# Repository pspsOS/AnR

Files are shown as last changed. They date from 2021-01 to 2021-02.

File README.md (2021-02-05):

# AnR: PSPS Avionics and Recovery GitHub
This document was last edited by Jeffrey Kaji on *4 Feb 2021*. <br/>
View our license [here](LICENSE)

## MITCH_2021
**Multi-Instrument Telemetry Computer Hardware** for PSPS 2021 Rocket<br> 
Important Macros: <br>
``getBit(A, X)`` : gets the *"Xth"* bit of *"A"*. _(By VV)_<br>
``setBit(A, X, V)`` : sets the *"Xth"* bit of *"A"* to *"V"*. _(By VV)_ <br><br>
Debuging Macros: <br>
``print()`` : Prints to console. Is disabled by ``NDEBUG``. Does not accept string formatters. _(By JK)_ <br>
``prints()`` : Prints to console. Is disabled by ``NDEBUG``. Requires string formatters. _(By JK)_ <br>
``printe()`` : Prints to error stream. Is disabled by ``NDEBUG``. Requires string formatters. _(By JK)_ <br>

#### Quick Links
* [Documentation Folder **Docs/**](../Docs/README.md)
* [**Recovery-Avionics Jira**](https://psps-recovery-avionics.atlassian.net/jira/software/projects/AV/boards/2)
* [**SRAD Software Confluence Page**](https://psps-recovery-avionics.atlassian.net/wiki/spaces/PSPS/pages/31457281/SRAD+Software)
* [**Task Flowcharts Google Drive Folder**](https://drive.google.com/drive/u/0/folders/1KGmiUlNgTaysgdSle6QIzn_O4cT77nek)
* [**Hardware Datasheets Google Drive Folder**](https://drive.google.com/drive/u/0/folders/14jC0XhoOVIF4Ko5ylgHbCWUhaxgak8n0)

---
**Creating a *README.md*?** <br />
 Try using this free online editor that makes it super easy: 
<https://jbt.github.io/markdown-editor/>

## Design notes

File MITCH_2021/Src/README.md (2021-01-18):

# Src
### Generated Project Files:
* [__freertos.c__](freertos.c)
* [__main.c__](main.c)
* [__stm32f4xx_hal_msp.c__](stm32f4xx_hal_msp.c)
* [__stm32f4xx_hal_timebase_tim.c__](stm32f4xx_hal_timebase_tim.c)
* [__stm32f4xx_it.c__](stm32f4xx_it.c)
* [__sysmem.c__](sysmem.c)
* [__system_stm32f4xx.c__](system_stm32f4xx.c)

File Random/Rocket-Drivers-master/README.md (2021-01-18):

# Rocket Drivers

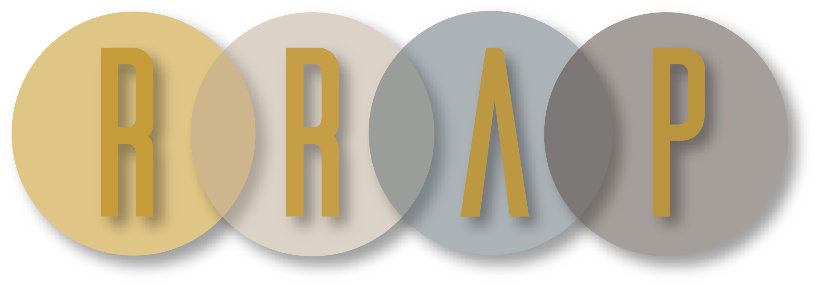
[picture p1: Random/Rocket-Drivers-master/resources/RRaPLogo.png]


This project contains files written to control the avionics platform for Reusable Rocketry at Purdue's gimbal based Atlas platform. The drivers are also intended for use in the Purdue Space Program's solid rocket program.

> ALL CODE IS PROVIDED AS IS. PLEASE READ THE LICENSE FOR MORE INFORMATION

## Timeline

- [x] Create generic SPI bus functions
- [X] Extract pressure, temperature, and altitude from onboard barometer
- [X] Extract (but not parse) NMEA strings from GPS
- [X] Extract linear accelerometer data
- [ ] Extract 9 axis IMU data

## Intended Hardware

These drivers are intended to be used in conjunction with 4 sensors. These sensors are:

- [MS5607-02BA03
Barometric Pressure Sensor](https://www.te.com/commerce/DocumentDelivery/DDEController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)
- [FGPMMOPA6H Standalone GPS Module](https://cdn-shop.adafruit.com/datasheets/GlobalTop-FGPMMOPA6H-Datasheet-V0A.pdf)
- [MMA655x Single Axis Inertial Sensor](https://www.nxp.com/docs/en/data-sheet/MMA655x.pdf)
- [ICM-20948 IMU](http://www.invensense.com/wp-content/uploads/2016/06/DS-000189-ICM-20948-v1.3.pdf)

## Notes

The struct `rocket_t` is my default data container. It should be changed to match whatever the intended plan for the rocket is. Doing this is simply easier from my end, so it isn't really a finalized solution. The calculations for the barometer are already included in the code. However, these would be worth going over again and starting to understand what they do and how they work. As for the GPS, the code will only return the NMEA strings GLL, GPRMC, and GPVTG (no sattelite count) unless something else is required. The command to change this frequency is 'PMTK_API_SET_NMEA_OUTPUT' and can be found [here](https://cdn-shop.adafruit.com/datasheets/PMTK_A11.pdf). The code will need to be changed to reflect the changes in output stings, but it shouldn't be too hard with the given code.

> `HandleHALError()` could be a very powerful tool for detecting issues. Since the target platform is unknown, it has been left blank. Please make sure to update this!

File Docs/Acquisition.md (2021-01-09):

# Acquisition
This document was last edited by Jeffrey Kaji on *5 Jan 2021*. <br/>

## Description
This is a documentation for the code supporting the task _Acquisition_. <br>
Created for use by Purdue Space Program Solids. <br><br>
[View][1] the _Task Flow Chart_. <br>

__Required Files:__
* [acquisition.h](../MITCH_2021/IncPSP/acquisition.h)
* [acquisition.c](../MITCH_2021/SrcPSP/acquisition.c)

[1]: https://drive.google.com/file/d/17b3zl4mSmjUOjUfPsQ9OTFR39xYNh1Iw/view?usp=sharing "Task Flow Chart (Read Only)"

## acquisition.h
_acquisition.h_ is a header file. A header file is a file with extension _.h_ which contains C function declarations and macro definitions to be shared between several source files. <br>
```c
// Parent Functions
void setup_A();
void loop_A();

// Setup
void gpsSetup_A();
void bmpSetup_A();
void imuSetup_A();
void alaSetup_A();

// Loop
void gpsRead_A();
void bmpRead_A();
void imuRead_A();
void checkStatus_A();
void sendUpdate_A();
``` 
The above is the main contents of _acquisition.h_. This declares all the functions created in _acquisition.c_.

## acquisition.c
_acquisition.c_ is a source file. A source file is a file with extension _.c_ that contains program instructions. <br> <br>
_acquisition.c_ acquires the raw data from the sensors and sends the data to processing via the global interface structs.

```c
/* Local variable declarations */
char gpsNmea[MAX_NMEA]; // Buffer that holds GPS String
bool daqScaling;        // Enables/Disables DAQ Scaling
ui8 daqScaler;          // DAQ Scaling number – Sets the ratio
bool gpsNominal;        // Indicates whether the GPS is nominal
bool bmpNominal;        // Indicates whether the BMP is nominal
bool imuNominal;        // Indicates whether the IMU is nominal
bool alaNominal;        // Indicates whether the ALA is nominal
bool sendDaqStatus;     // Indicates whether to update the daqStatusData struct
ui8 gpsCounter;         // Counter used in DAQ Scaling for Finite State Machine
ui8 bmpCounter;         // Counter used in DAQ Scaling for Finite State Machine
ui8 fsmState;           // Defines state of Finite State Machine

// Used for parsing NMEA data
ui8 _nmeaAddrStart;
ui8 _nmeaAddrEnd;

// File pointers for Debugging
#ifndef NDEBUG
	FILE *_gpsFile;
	FILE *_bmpFile;
	FILE *_imuFile;
	FILE *_alaFile;
#endif
```
The above declares the local variables. Listed below are the current variables:
* __gpsNmea[MAX_NMEA]__ is a character array (string) that holds the latest read from the GPS sensor. It is then parsed and passed to Processing by the function __gpsRead_A()__ via the struct __g_gpsData__. The constant __MAX_NMEA__ is defined in the header file [__common.h__](Common.md).
* __daqScaling__ is true when DAQ Scaling is enabled. DAQ Scaling makes _Acquisition_ act as a finite state machine, making measurments across the different sensors at different rates. 
* __daqScaler__ determines the ratios of data acquisition between each of the sensors. Let __daqScaler = n__ and assume DAQ Scaling is enabled. For each GPS measurment, _Acquisition_ will take __n__ BMP measurments and __n<sup>2</sup>__ IMU measurements.
* __gpsNominal__ is true if connection with the GPS has been established and if it is acting nominally.
* __bmpNominal__ is true if connection with the BMP has been established and if it is acting nominally.
* __imuNominal__ is true if connection with the IMU has been established and if it is acting nominally.
* __alaNominal__ is true if connection with the ALA has been established and if it is acting nominally.
* __sendDaqStatus__ is true if the DAQ Status struct should be updated.
* __gpsCounter__ is TBD
* __bmpCounter__ is TBD
* __fsmState__ is TBD
* **_nmeaAddrStart** is used when parsing NMEA strings. It stores the start index of a specific element within the string and is set by the the function [**_findNmeaAddr(int addr)**](###_findNmeaAddr(int-addr)).
*  **_nmeaAddrEnd** is used when parsing NMEA strings. It stores the end index of a specific element within the string and is set by the the function [**_findNmeaAddr(int addr)**](###_findNmeaAddr(int-addr)).
*  **_gpsFile** is a file pointer to the text file that has test data for the GPS. This is only declared if **NDEBUG** is not defined.
*  **_bmpFile** is a file pointer to the text file that has test data for the BMP. This is only declared if **NDEBUG** is not defined.
*  **_imuFile** is a file pointer to the text file that has test data for the IMU. This is only declared if **NDEBUG** is not defined.
*  **_alaFile** is a file pointer to the text file that has test data for the ALA. This is only declared if **NDEBUG** is not defined.
<br><br>

### setup_A()
```c
void setup_A() {

	// Initialize local variables
	daqScaling = false;
	daqScaler = DEFAULT_DAQ_SCALER;
	gpsNominal = false;
	bmpNominal = false;
	imuNominal = false;
	alaNominal = false;
	sendDaqStatus = false;
	gpsCounter = 0;
	bmpCounter = 0;
	fsmState = ACQUIRE_IMU_BMP_GPS;

	// Setup sensors
	gpsSetup_A();
	bmpSetup_A();
	imuSetup_A();
	alaSetup_A();

	// Unlock initialized interface structs
	g_daqStatusData.lock = false;
	g_daqScalingData.lock = false;
	
	// Send update
	sendUpdate_A();
}
```
The above function is the one-time setup function for _acquisition.c_. This function has different sections, each denoted by their own comment header. <br>
#### Intialize local variables
In this section, all local variables are initialized as needed.
```c
	daqScaling = false;
	daqScaler = DEFAULT_DAQ_SCALER;
```
> DAQ Scaling is disabled on startup. The DAQ Scaler is set to the default value constant which is defined in common.h.
<br><br>

```c
	gpsNominal = false;
	bmpNominal = false;
	imuNominal = false;
	alaNominal = false;
```
> All _"sensor nominal"_ variables are set to false. Each variable will be set to true once a connection to its sensor is established.
<br><br>

```c
	sendDaqStatus = false;
```
> Since __setup_A()__ already updates the DAQ Status interface struct, __sendDaqStatus__ is initially set to false.
<br><br>

```c
	gpsCounter = 0;
	bmpCounter = 0;
	fsmState = ACQUIRE_IMU_BMP_GPS;
```
> Finite state machine variables. TBD
<br><br>

#### Setup sensors
In this section, each sensor is setup by calling their setup functions.
```c
	gpsSetup_A();
	bmpSetup_A();
	imuSetup_A();
	alaSetup_A();
```

#### Unlock initialized interface structs
In this section, the initialized global interface structs used by _Acquisition_ are unlocked, insuring they can be accessed.
```c
	g_daqStatusData.lock = false;
	g_daqScalingData.lock = false;
```
#### Send update
The DAQ Scaling Status struct is updated via the function [__sendUpdate_A()__](###sendUpdate_A()).
```c
	sendUpdate_A();
```
<br>

### loop_A()
TBD
<br><br>

### gpsSetup_A()
```c
void gpsSetup_A() {
	#ifndef NDEBUG
		_gpsFile = setupSensorFile_DS(GPS, &gpsNominal);
	#else
		// TODO: Implement gpsSetup
	#endif
}
```
The above function sets up the GPS sensor. If **NDBEUG** is defined (Debug Mode), **_gpsFile** is set using the function **setupSensorFile_DS** which is declared in the **debugSettings**. If **NDEBUG** is not defined, *TODO*.
<br><br>

### bmpSetup_A()
```c
void bmpSetup_A() {
	#ifndef NDEBUG
		_bmpFile = setupSensorFile_DS(BMP, &bmpNominal);
	#else
		// TODO: Implement bmpSetup
	#endif
}
```
The above function sets up the BMP sensor. If **NDBEUG** is defined (Debug Mode), **_bmpFile** is set using the function **setupSensorFile_DS** which is declared in the **debugSettings**. If **NDEBUG** is not defined, *TODO*.
<br><br>

### imuSetup_A()

```c
void imuSetup_A() {
	#ifndef NDEBUG
		_imuFile = setupSensorFile_DS(IMU, &imuNominal);
	#else
		// TODO: Implement imuSetup
	#endif
}
```
The above function sets up the IMU sensor. If **NDBEUG** is defined (Debug Mode), **_imuFile** is set using the function **setupSensorFile_DS** which is declared in the **debugSettings**. If **NDEBUG** is not defined, *TODO*.
<br><br>

### alaSetup_A()
```c
void alaSetup_A() {
	#ifndef NDEBUG
		_alaFile = setupSensorFile_DS(ALA, &alaNominal);
	#else
		// TODO: Implement alaSetup
	#endif
}
```
The above function sets up the ALA sensor. If **NDBEUG** is defined (Debug Mode), **_alaFile** is set using the function **setupSensorFile_DS** which is declared in the **debugSettings**. If **NDEBUG** is not defined, *TODO*.
<br><br>

### gpsRead_A()
TBD
<br><br>

### bmpRead_A()
TBD
<br><br>

### imuRead_A()
TBD
<br><br>

### checkStatus_A()
```c
void checkStatus_A() {
	// Check for daqScaling update
	while(g_daqScalingData.lock) {
		retryTakeDelay(0);
	}
	g_daqScalingData.lock = true;
	if(g_daqScalingData.hasUpdate) {
		daqScaling = g_daqScalingData.enableDaqScaling;
		g_daqScalingData.hasUpdate = false;
		sendDaqStatus = true;
	}
	g_daqScalingData.lock = false;

	// GPS handling
	if(!gpsNominal) {
		gpsSetup_A();
		if(gpsNominal) {
			sendDaqStatus = true;
		}
	}

	// BMP Handling
	if(!bmpNominal) {
		bmpSetup_A();
		if(bmpNominal) {
			sendDaqStatus = true;
		}
	}

	// IMU Handling
	if(!imuNominal) {
		imuSetup_A();
		if(imuNominal) {
			sendDaqStatus = true;
		}
	}

	// ALA Handling
	if(!alaNominal) {
		alaSetup_A();
		if(alaNominal) {
			sendDaqStatus = true;
		}
	}

	// Send update if needed
	if(sendDaqStatus) {
		sendUpdate_A();
	}
}
```
The above function is exceuted in between sensor data acquisitions and handles settings and sensor updates. This function has different sections, each denoted by their own comment header. <br>
#### Check for daqScaling update
In this section, the global struct g_daqScalingData is checked to see if the local variable should be updated.
```c
	while(g_daqScalingData.lock) {
		retryTakeDelay(0);
	}
    g_daqScalingData.lock = true;
```
> Wait for global struct to be unlocked, then lock it immediately when available.
<br><br>

```c
	if(g_daqScalingData.hasUpdate) {
		daqScaling = g_daqScalingData.enableDaqScaling;
		g_daqScalingData.hasUpdate = false;
		sendDaqStatus = true;
	}
```
> If g_daqScalingData has an update, set the local __daqScaling__ variable to the value of g_daqScalingData.**enableDaqScaling**. <br>
> Then, g_daqScalingData.**hasUpdate** is set to false, indicating that the update has been read and addressed.<br>
> Lastly, the local variable __sendDaqStatus__ is set to true, signifying that there has been an update to the DAQ Status. 
<br><br>

```c
	g_daqScalingData.lock = false;
```
> The global struct is unlocked again.
<br><br>

#### GPS, BMP, IMU and ALA handling 
In these four sections,

### _A()
TBD
<br><br>

### gpsSetup_A())
<br><br><br><br><br><br><br><br><br><br><br><br>

### sendUpdate_M()
```c
void sendUpdate_M() {
	while(g_acquisitionData.lock) {
		retryTakeDelay(0);
	}
	g_acquisitionData.lock = true;
	g_acquisitionData.timeStamp = getTimeStamp();
	g_acquisitionData.batteryVoltage;
	for (ui8 i = 0; i < 4; i++) {
		g_acquisitionData.continuity[i] = continuity[i];
	}
	g_acquisitionData.buttonState = buttonState;
	g_acquisitionData.hardwareDeploymentDisable = hardwareDeploymentDisable;
	g_acquisitionData.hasUpdate = true;
	g_acquisitionData.lock = false;
}
``` 
The above function handles sending the _acquisition.c_ data to other files. To accomplish this, the function stores all local data as global variables which can be accessed by other files. These globals include:
* __g_acquisitionData.batteryVoltage__ is the value of the voltage departing from the battery. It is being detected from _TBD_ on the PCB.
* __g_acquisitionData.continuity[4]__ is a bool array which checks the continuity connection of the 4 parachute deployment charges. It is detected from the _Sense_A-D_ signals on the PCB.
* __g_acquisitionData.buttonState__ detects the state of the switch on the hardware. This switch _TBD_
* __g_acquisitionData.hardwareDeploymentDisable__ detects if the hardware disable terminal block system is enabled or disabled. During actual flight (or when we want parachute charges to deploy), the connection between the terminal block should be severed.
* __g_acquisitionData.hasUpdate__ tells other files if the data has an update from previous access.
* __g_acquisitionData.lock__ prevents multiple files from accessing the global variables at the same time by "locking" the globals while writing or reading.

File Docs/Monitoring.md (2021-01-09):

# Monitoring
This document was last edited on *4 Jan 2021*. <br/>

### Description
This is a documentation for the code supporting the task _Monitoring_. <br>
Created for use by Purdue Space Program Solids. <br><br>
[View][1] the _Task Flow Chart_. <br>

### Required Files:
* [monitoring.h](../MITCH_2021/IncPSP/monitoring.h)
* [monitoring.c](../MITCH_2021/SrcPSP/monitoring.c)

[1]: https://drive.google.com/file/d/1L-hbviqYfiP9NwsLlXdcOAHZ8kLTNxf0/view?usp=sharing "Task Flow Chart (Read Only)"

## monitoring.h
_monitoring.h_ is a header file. A header file is a file with extension _.h_ which contains C function declarations and macro definitions to be shared between several source files. <br>
```c
void setup_M();
void loop_M();
void checkBatteryVoltage();
void checkContinuity();
void checkButtonState();
void checkHardwareDeploymentDisable_M();
void sendUpdate_M();
``` 
The above is the main contents of _monitoring.h_. This declares all the functions created in _monitoring.c_.

## monitoring.c
_monitoring.c_ is a source file. A source file is a file with extension _.c_ that contains program instructions. <br> <br>
_monitoring.c_ gathers data for the voltage of the battery, the continuity of the parachute deployment charges, the state of the button, and the state of the hardware charge disable which it stores as global variables for other files to access.

```c
float batteryVoltage; // Voltage of battery (V)
bool continuity[4]; // Continuity status of parachute deployment charges
bool buttonState; // State of button (on/off)
bool hardwareDeploymentDisable; // Terminal block disables deployment in hardware
```
The above declares the local variables. Listed below are the current variables:
* __batteryVoltage__ is the value of the voltage departing from the battery. It is being detected from _TBD_ on the PCB.
* __continuity[4]__ is a bool array which checks the continuity connection of the 4 parachute deployment charges. It is detected from the _Sense_A-D_ signals on the PCB.
* __buttonState__ detects the state of the switch on the hardware. This switch _TBD_
* __hardwareDeploymentDisable__ detects if the hardware disable terminal block system is enabled or disabled. During actual flight (or when we want parachute charges to deploy), the connection between the terminal block should be severed.

### setup_M()
```c
void setup_M() {
	//initialize variables
	#ifndef NDEBUG
		_monitoringFile = setupMonitoringFile_DS();
	#else
		// TODO: Implement Monitoring Setup
	#endif
	batteryVoltage = 7.4;
	for (ui8 i = 0; i < 4; i++) {
		continuity[i] = true;
	}
	buttonState = false;
	hardwareDeploymentDisable = false;
}
```
The above function is the one-time setup function for _monitoring.c_. This function only initializes local variables.

### loop_M()
```c
void loop_M() {
	#ifndef NDEBUG
		if(!simulateMonitoring) {
			if(notifyWhenReadAborted)
				print("Monitoring read aborted.\n");
			return;
		}
		fscanf(_monitoringFile, "%f", &batteryVoltage);
		fscanf(_monitoringFile, "%d", &continuity[0]);
		fscanf(_monitoringFile, "%d", &continuity[1]);
		fscanf(_monitoringFile, "%d", &continuity[2]);
		fscanf(_monitoringFile, "%d", &continuity[3]);
		fscanf(_monitoringFile, "%d", &buttonState);
		fscanf(_monitoringFile, "%d", &hardwareDeploymentDisable);
	#else
		checkBatteryVoltage_M();
		checkContinuity_M();
		checkButtonState_M();
		checkHardwareDeploymentDisable_M();
	#endif
	sendUpdate_M();
}
```
The above function is the flight loop function which will run continuously during flight. When in debug mode, the function will read data from a _.txt_ file. When not in debug mode, the function will call other functions to gather the necessary monitoring data.

### checkBatteryVoltage_M()
```c
void checkBatteryVoltage_M() {
	// TODO: Implement battery voltage reading from hardware
}
``` 
_TBD_

### checkContinuity_M()
```c
void checkContinuity_M() {
	for (ui8 i = 0; i < 4; i++) {
		// TODO: Implement continuity reading from hardware
	}
}
``` 
_TBD_

### checkButtonState_M()
```c
void checkButtonState_M() {
	// TODO: Implement button state reading from hardware
}
``` 
_TBD_

### checkHardwareDeploymentDisable_M()
```c
void checkHardwareDeploymentDisable_M() {
	// TODO: Implement hardware deployment disable reading from hardware
}
``` 
_TBD_

### sendUpdate_M()
```c
void sendUpdate_M() {
	while(g_monitoringData.lock) {
		retryTakeDelay(0);
	}
	g_monitoringData.lock = true;
	g_monitoringData.timeStamp = getTimeStamp();
	g_monitoringData.batteryVoltage;
	for (ui8 i = 0; i < 4; i++) {
		g_monitoringData.continuity[i] = continuity[i];
	}
	g_monitoringData.buttonState = buttonState;
	g_monitoringData.hardwareDeploymentDisable = hardwareDeploymentDisable;
	g_monitoringData.hasUpdate = true;
	g_monitoringData.lock = false;
}
``` 
The above function handles sending the _monitoring.c_ data to other files. To accomplish this, the function stores all local data as global variables which can be accessed by other files. These globals include:
* __g_monitoringData.batteryVoltage__ is the value of the voltage departing from the battery. It is being detected from _TBD_ on the PCB.
* __g_monitoringData.continuity[4]__ is a bool array which checks the continuity connection of the 4 parachute deployment charges. It is detected from the _Sense_A-D_ signals on the PCB.
* __g_monitoringData.buttonState__ detects the state of the switch on the hardware. This switch _TBD_
* __g_monitoringData.hardwareDeploymentDisable__ detects if the hardware disable terminal block system is enabled or disabled. During actual flight (or when we want parachute charges to deploy), the connection between the terminal block should be severed.
* __g_monitoringData.hasUpdate__ tells other files if the data has an update from previous access.
* __g_monitoringData.lock__ prevents multiple files from accessing the global variables at the same time by "locking" the globals while writing or reading.

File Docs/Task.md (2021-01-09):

# Task
This document was last edited by Person on *D Mon. YYYY*. <br/>

## Description
This is a documentation for the code supporting the task _Task_. <br>
Created for use by Purdue Space Program Solids. <br><br>
[View][1] the _Task Flow Chart_. <br>

__Required Files:__
* [task.h](../MITCH_2021/IncPSP/task.h)
* [task.c](../MITCH_2021/SrcPSP/task.c)

## task.h
_task.h_ is a header file. A header file is a file with extension _.h_ which contains C function declarations and macro definitions to be shared between several source files. <br>
```c
void setup();
void function2();
``` 
The above is the main contents of _task.h_. This declares all the functions created in _task.c_.

## task.c
_task.c_ is a source file. A source file is a file with extension _.c_ that contains program instructions. <br> <br>
_task.c_ acquires the raw data from the sensors and sends the data to processing via the global interface structs.

```c
float var1[4]      // Array of floats that is 4 long
bool var2;         // bool that keeps track of something
ui8 var3;          // Comments like these are great
```
The above declares the local variables. Listed below are the current variables:
* __var1[4]__ is an array of floats that keeps track of something. An explanation would be defined here.
* __var2__ is a bool that keeps track of something else.
* __var3__ is a ui8 which is a 8 bit unsigned int. If it is relevant to mention that it is used later in [function2](###function2), then linking to it like this is a good way to indicate that fact.

### setup()
```c
void setup() {
	//initialize variables
	for(int i = 0; i < 4; i++)
    	var1[i] = i * 3.4;
    var2 = false;
    var3 = 29;
}
```
Each function should be isolated and described in one or more paragraphs, making its use clear. For example: <br> 
The above function is the one-time setup function for _task.c_. This function only initializes local variables.

### function2()
```c
void function2() {
	var3 = !var3;
}
```
The above function is linked to earlier in the document. You can use links to increase readability.

<!--- You can make an list of links at the end of a file like the one below. This makes it so there isn't a giant link in the middle of your text-->

[1]: https://drive.google.com/file/d/17b3zl4mSmjUOjUfPsQ9OTFR39xYNh1Iw/view?usp=sharing "Task Flow Chart (Read Only)"

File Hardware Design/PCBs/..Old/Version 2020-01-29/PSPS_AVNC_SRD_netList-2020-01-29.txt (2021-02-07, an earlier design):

Netlist

Exported from PSPS_AVNC_SRD_fullBoard-2020-01-29.sch at 1/29/2020 1:42 PM

EAGLE Version 9.5.1 Copyright (c) 1988-2019 Autodesk, Inc.

Net         Part     Pad      Pin        Sheet

1V8         C2-0S    1        1          1
            C2-1S    1        1          1
            C3-1S    1        1          1
            D1-1S    A        A          1
            L1-0S    2        2          1
            U0-S     4        FB         1
            U1-S     13       VDD        1
            U1-S     8        VDDIO      1
            U12-S    5        VCC        1
            U13-S    5        VCC        1
            U14-S    5        VCC        1

3D-FIX      D3-4S    A        A          1
            U4-S     5        3D-FIX     1

3V3         C1-0S    1        1          1
            C1-2S    1        1          1
            C1-3S    1        1          1
            D1-2S    A        A          1
            D1-3S    A        A          1
            D1-4S    A        A          1
            U0-S     1        VI         1
            U0-S     3        EN         1
            U11-S    5        VCC        1
            U2-S     9        VCC        1
            U3-S     P$1      VDD        1
            U4-S     1        VCC        1

CLK         U13-S    2        A          1
            U2-S     10       SCLK       1
            U3-S     P$8      SCLK       1

CLK_1V8     U1-S     23       SCL/SCLK   1
            U13-S    4        Y          1

CS1         U14-S    2        A          1

CS1_1V8     U1-S     22       NCS        1
            U14-S    4        Y          1

CS2         U2-S     12       CS         1

CS3         U3-S     P$4      CSB        1
            U3-S     P$5      CSB        1

D1-1S_R1-1S D1-1S    C        C          1
            R1-1S    1        1          1

D1-2S_R1-2S D1-2S    C        C          1
            R1-2S    1        1          1

D1-3S_R1-3S D1-3S    C        C          1
            R1-3S    1        1          1

D1-4S_R1-4S D1-4S    C        C          1
            R1-4S    1        1          1

D1A-S_R1A-S D1A-S    C        C          1
            R1A-S    1        1          1

D1B-S_R1B-S D1B-S    C        C          1
            R1B-S    1        1          1

D2-1S_R2-1S D2-1S    C        C          1
            R2-1S    1        1          1

D2-2S_R2-2S D2-2S    C        C          1
            R2-2S    1        1          1

D2-3S_R2-3S D2-3S    C        C          1
            R2-3S    1        1          1

D2-4S_R2-4S D2-4S    C        C          1
            R2-4S    1        1          1

D2A-S_R2A-S D2A-S    C        C          1
            R2A-S    1        1          1

D2B-S_R2B-S D2B-S    C        C          1
            R2B-S    1        1          1

D3-4S_R3-4S D3-4S    C        C          1
            R3-4S    1        1          1

ERROR       D2A-S    A        A          1
            D2B-S    A        A          1

EX_ANT      AT1-S    1        SIGNAL     1
            U4-S     11       EX_ANT     1

GND         AT1-S    2        GND_1      1
            AT1-S    3        GND_2      1
            AT1-S    4        GND_3      1
            C1-0S    2        2          1
            C1-1S    2        2          1
            C1-2S    2        2          1
            C1-3S    2        2          1
            C2-0S    2        2          1
            C2-1S    2        2          1
            C2-2S    2        2          1
            C3-1S    2        2          1
            C3-2S    2        2          1
            R1-1S    2        2          1
            R1-2S    2        2          1
            R1-3S    2        2          1
            R1-4S    2        2          1
            R1A-S    2        2          1
            R1B-S    2        2          1
            R2-1S    2        2          1
            R2-2S    2        2          1
            R2-3S    2        2          1
            R2-4S    2        2          1
            R2A-S    2        2          1
            R2B-S    2        2          1
            R3-4S    2        2          1
            U0-S     2        GND        1
            U1-S     18       GND        1
            U1-S     20       RESV.GND   1
            U11-S    3        GND        1
            U12-S    3        GND        1
            U13-S    3        GND        1
            U14-S    3        GND        1
            U2-S     13       VSSA       1
            U2-S     16       VSSA       1
            U2-S     2        VSS        1
            U2-S     4        VSS        1
            U2-S     7        VPP        1
            U3-S     P$2      PS         1
            U3-S     P$3      GND        1
            U4-S     12       GND        1
            U4-S     19       GND        1
            U4-S     3        GND        1
            U4-S     8        GND        1

MASTER_RX   U4-S     9        TX         1

MASTER_TX   U4-S     10       RX         1

MISO        U11-S    4        Y          1
            U2-S     8        MISO       1

MISO_1V8    U1-S     9        SDO/AD0    1
            U11-S    2        A          1

MOSI        U12-S    2        A          1
            U2-S     11       MOSI       1
            U3-S     P$6      SDO        1
            U3-S     P$7      SDI        1

MOSI_1V8    U1-S     24       SDA/SDI    1
            U12-S    4        Y          1

NOMINAL     D1A-S    A        A          1
            D1B-S    A        A          1

REGOUT      C1-1S    1        1          1
            U1-S     10       REGOUT     1

SW          L1-0S    1        1          1
            U0-S     5        SW         1

U1-CHECK    D2-1S    A        A          1

U2-CHECK    D2-2S    A        A          1

U3-CHECK    D2-3S    A        A          1

U4-CHECK    D2-4S    A        A          1

VREG        C2-2S    1        1          1
            U2-S     3        VREG       1

VREGA       C3-2S    1        1          1
            U2-S     1        VREGA      1

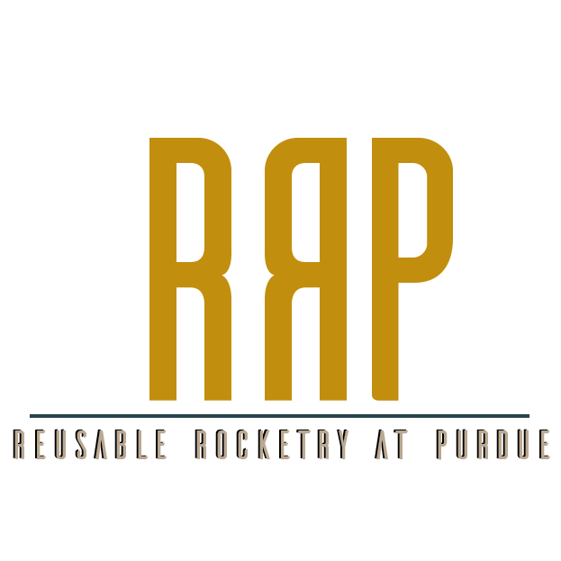
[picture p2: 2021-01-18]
Random/Rocket-Drivers-master/resources/RRaPTransCropped.png

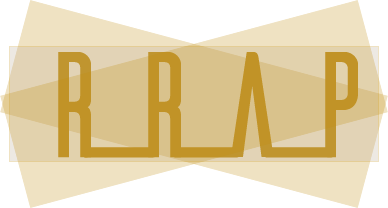
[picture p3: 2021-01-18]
Random/Rocket-Drivers-master/resources/VintageOne.png

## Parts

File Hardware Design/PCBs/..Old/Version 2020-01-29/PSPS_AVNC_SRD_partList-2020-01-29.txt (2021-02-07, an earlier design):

Partlist

Exported from PSPS_AVNC_SRD_fullBoard-2020-01-29.sch at 1/29/2020 1:40 PM

EAGLE Version 9.5.1 Copyright (c) 1988-2019 Autodesk, Inc.

Assembly variant: 

Part     Value          Device          Package                      Library        Sheet

AT1-S    A-1JB          A-1JB           A1JB                         SamacSys_Parts 1
C1-0S    4.7uF          C-USC0805       C0805                        resistor       1
C1-1S    0.1uF          C-USC0805       C0805                        resistor       1
C1-2S    0.1uF          C-USC0805       C0805                        resistor       1
C1-3S    0.1uF          C-USC0805       C0805                        resistor       1
C2-0S    10uF           C-USC0805       C0805                        resistor       1
C2-1S    0.1uF          C-USC0805       C0805                        resistor       1
C2-2S    1uF            C-USC0805       C0805                        resistor       1
C3-1S    0.1uF          C-USC0805       C0805                        resistor       1
C3-2S    1uF            C-USC0805       C0805                        resistor       1
D1-1S    Green          LEDCHIPLED_0805 CHIPLED_0805                 adafruit       1
D1-2S    Green          LEDCHIPLED_0805 CHIPLED_0805                 adafruit       1
D1-3S    Green          LEDCHIPLED_0805 CHIPLED_0805                 adafruit       1
D1-4S    Green          LEDCHIPLED_0805 CHIPLED_0805                 adafruit       1
D1A-S    Blue           LEDCHIPLED_0805 CHIPLED_0805                 adafruit       1
D1B-S    Blue           LEDCHIPLED_0805 CHIPLED_0805                 adafruit       1
D2-1S    Blue           LEDCHIPLED_0805 CHIPLED_0805                 adafruit       1
D2-2S    Blue           LEDCHIPLED_0805 CHIPLED_0805                 adafruit       1
D2-3S    Blue           LEDCHIPLED_0805 CHIPLED_0805                 adafruit       1
D2-4S    Blue           LEDCHIPLED_0805 CHIPLED_0805                 adafruit       1
D2A-S    Red            LEDCHIPLED_0805 CHIPLED_0805                 adafruit       1
D2B-S    Red            LEDCHIPLED_0805 CHIPLED_0805                 adafruit       1
D3-4S    Yellow         LEDCHIPLED_0805 CHIPLED_0805                 adafruit       1
L1-0S    10 uH          L-US            0805                         Computer2      1
R1-1S    TBD            R-US_R0805      R0805                        resistor       1
R1-2S    TBD            R-US_R0805      R0805                        resistor       1
R1-3S    TBD            R-US_R0805      R0805                        resistor       1
R1-4S    TBD            R-US_R0805      R0805                        resistor       1
R1A-S    TBD            R-US_R0805      R0805                        resistor       1
R1B-S    TBD            R-US_R0805      R0805                        resistor       1
R2-1S    TBD            R-US_R0805      R0805                        resistor       1
R2-2S    TBD            R-US_R0805      R0805                        resistor       1
R2-3S    TBD            R-US_R0805      R0805                        resistor       1
R2-4S    TBD            R-US_R0805      R0805                        resistor       1
R2A-S    TBD            R-US_R0805      R0805                        resistor       1
R2B-S    TBD            R-US_R0805      R0805                        resistor       1
R3-4S    TBD            R-US_R0805      R0805                        resistor       1
U0-S     TPS62202       TPS62202        SOT95P280X145-5              Computer2      1
U1-S     ICM-20948      ICM-20948       QFN40P300X300X105-25T159X175 Computer2      1
U2-S     MMA6555        MMA655X         QFN100P600X600X198-17T424N   Computer2      1
U3-S     MS5607         MS5607          MS5607                       Computer2      1
U4-S     FGPMMOPA6H     FGPMMOPA6H      SOIC127P1800X470-20N         Computer2      1
U11-S    SN74LV1T34     SN74LV1T34      SOT65P210X110-5              Computer2      1
U12-S    SN74LV1T34     SN74LV1T34      SOT65P210X110-5              Computer2      1
U13-S    SN74LV1T34     SN74LV1T34      SOT65P210X110-5              Computer2      1
U14-S    SN74LV1T34     SN74LV1T34      SOT65P210X110-5              Computer2      1

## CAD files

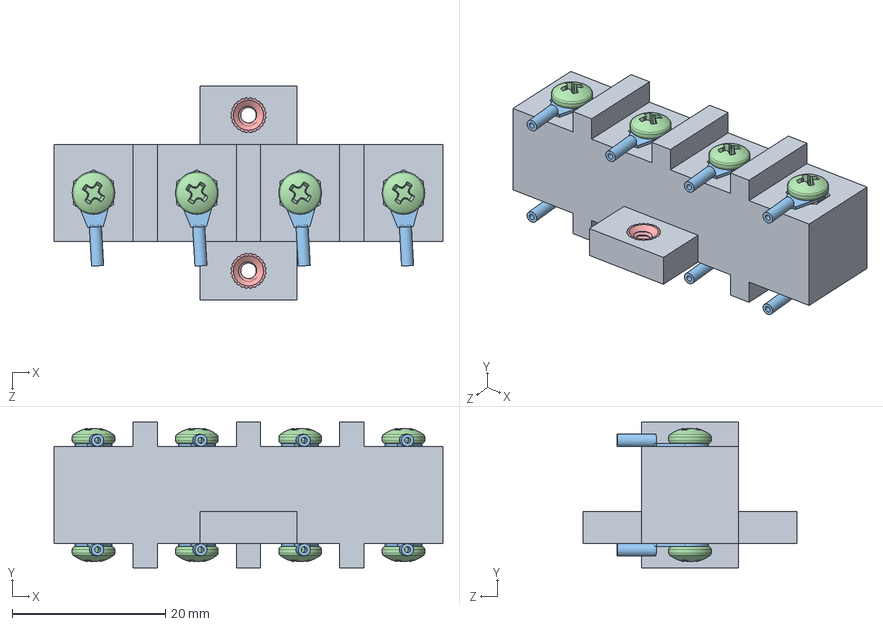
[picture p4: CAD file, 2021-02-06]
Hardware Design/CAD - Avionics Bay/BLTN-102-006 (Wire Passthrough)/BLTN-102-006-000.SLDASM
50.8 x 19.1 x 27.9 mm
BLTN-102-006-001
91115A509_18-8 SS FEM THRDED HEX STANDOFF x 4
BLTN-102-006-002 x 8
91772A106_18-8 SS PAN HEAD PHILLIPS MACHINE SCREW x 8
94459A250_BRASS HEAT-SET INSERT FOR PLASTIC x 2

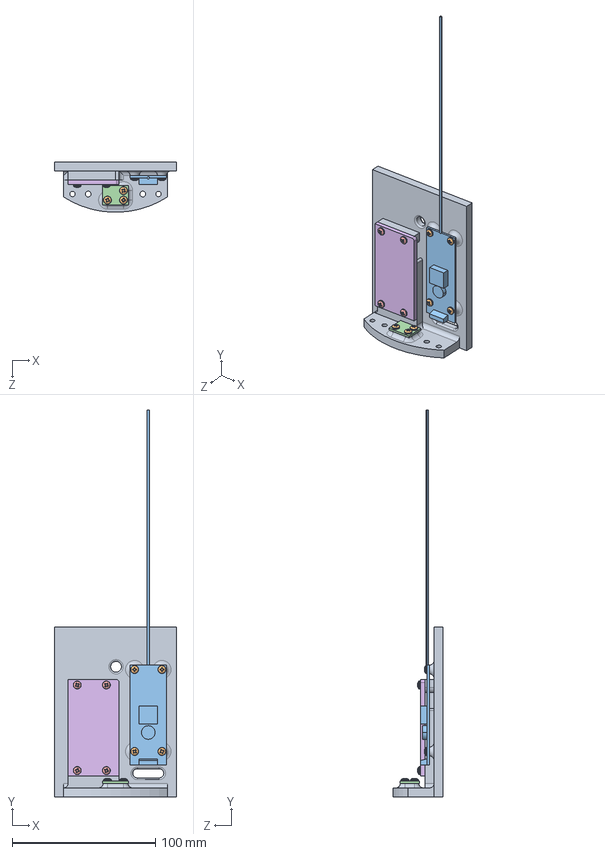
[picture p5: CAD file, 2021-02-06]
Hardware Design/CAD - Avionics Bay/BLTN-102-001 (Telemetrum Card)/BLTN-102-001-000.SLDASM
85.1 x 269.9 x 35.1 mm
BLTN-102-001-001
91249A108_BLACK-OXIDE FNSH PAN HEAD PHIL MACHINE SCREW x 7
BLTN-102-001-002
BLTN-102-001-003
91249A115_BLACK-OXIDE FNSH PAN HEAD PHIL MACHINE SCREW x 4
BLTN-102-001-004
93365A120_HEAT-SET INSERTS FOR PLASTICS x 11

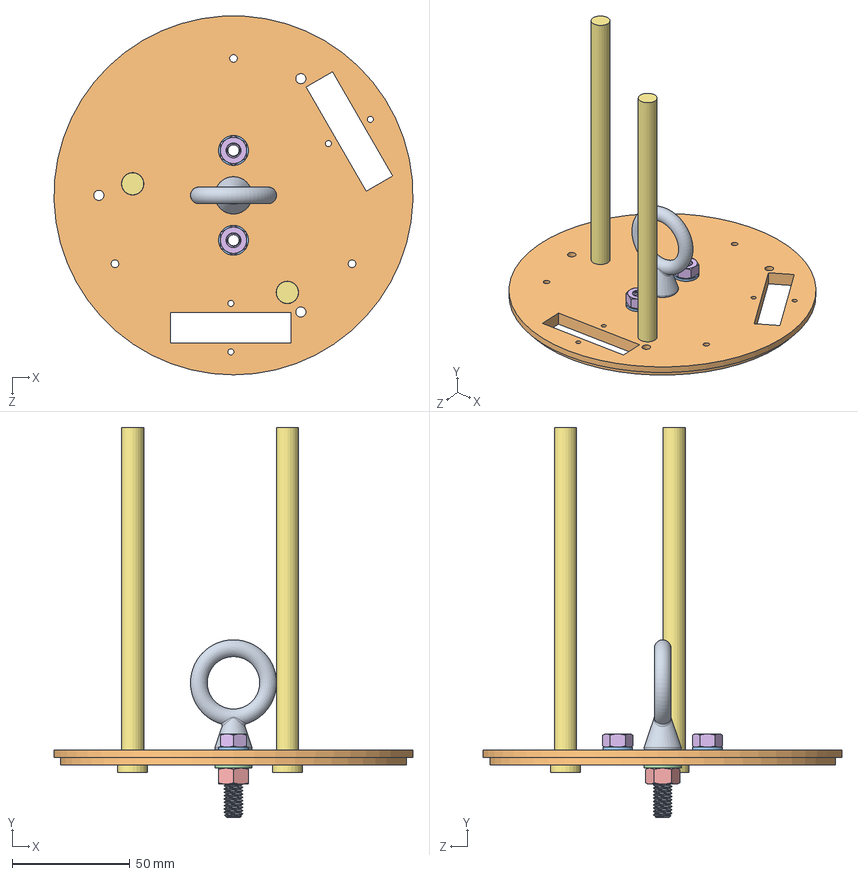
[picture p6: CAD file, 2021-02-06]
Hardware Design/CAD - Avionics Bay/BLTN-102-004 (Fwd Bulkhead)/BLTN-102-004-000.SLDASM
152.3 x 165.5 x 152.2 mm
BLTN-102-004-001
BLTN-102-004-002
BLTN-102-004-007 x 2
BLTN-102-004-006
BLTN-102-004-005
BLTN-102-004-004 x 2
BLTN-102-004-003 x 2

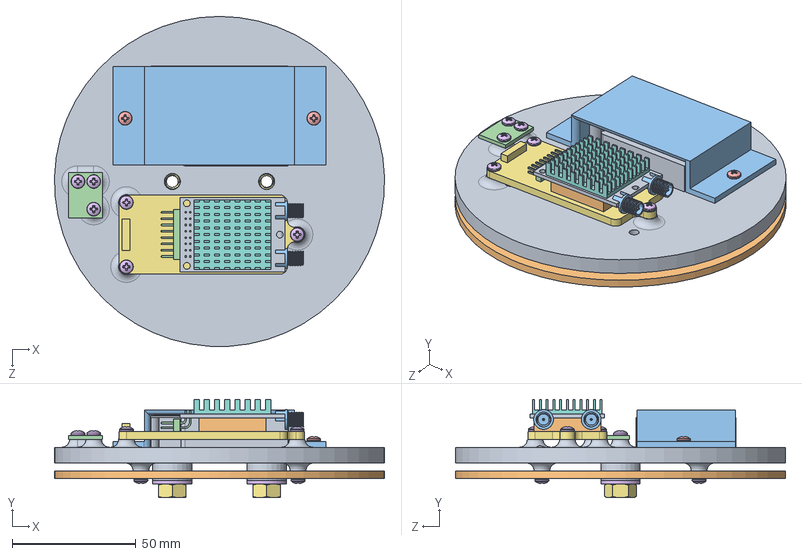
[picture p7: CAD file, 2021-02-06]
Hardware Design/CAD - Avionics Bay/BLTN-102-005 (SRAD Sled)/BLTN-102-005-000.SLDASM
133.3 x 39.7 x 133.4 mm
BLTN-102-005-001
BLTN-102-005-005
BLTN-102-005-002
BLTN-102-005-006
94459A250_BRASS HEAT-SET INSERT FOR PLASTIC x 12
91249A108_BLACK-OXIDE FNSH PAN HEAD PHIL MACHINE SCREW x 10
BLTN-102-005-004
RFD900 Heat Sink.CATPart
RFD900 PCB.CATPart
RFD900 RF Shield.CATPart
RFD900 Antenna Header.CATPart x 2
RFD900 Header Pins.CATPart
91249A105_BLACK-OXIDE FNSH PAN HEAD PHIL MACHINE SCREW x 2
92141A029_TYPE 18-8 STAINLESS STEEL FLAT WASHER x 2
95462A029_GRADE 5 STEEL HEX NUT x 2

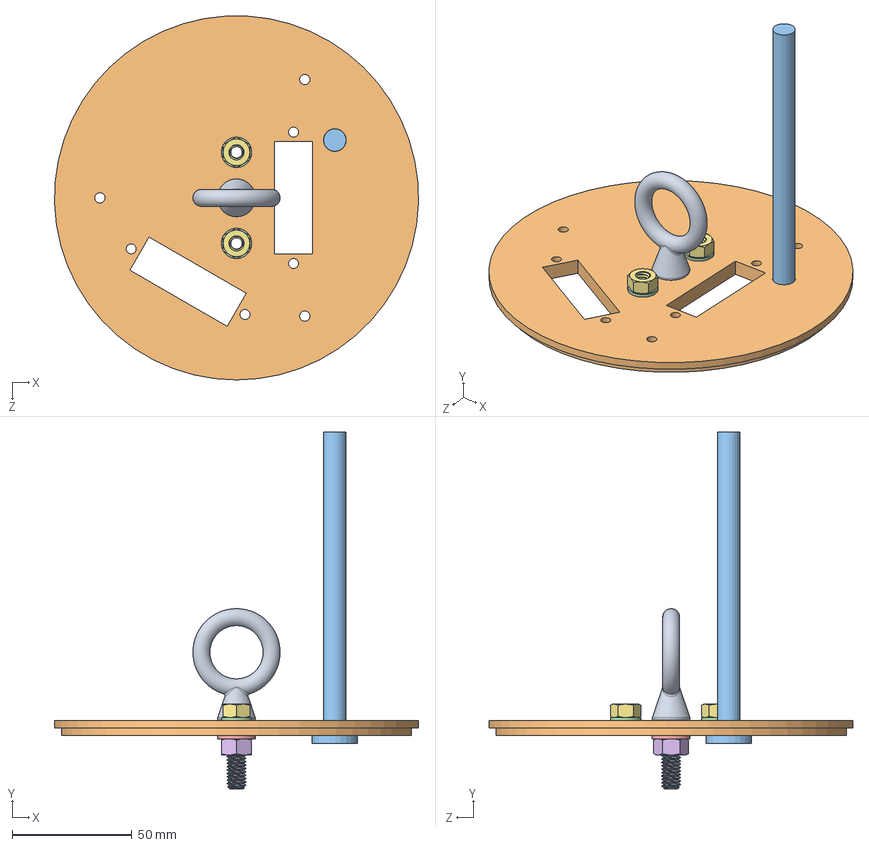
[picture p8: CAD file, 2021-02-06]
Hardware Design/CAD - Avionics Bay/BLTN-102-004 (Fwd Bulkhead)/BLTN-102-004-001.SLDASM
152.3 x 149.2 x 152.2 mm
BLTN-102-004-008
BLTN-102-004-002
BLTN-102-004-003
BLTN-102-004-007 x 2
BLTN-102-004-006
BLTN-102-004-005
BLTN-102-004-004 x 2

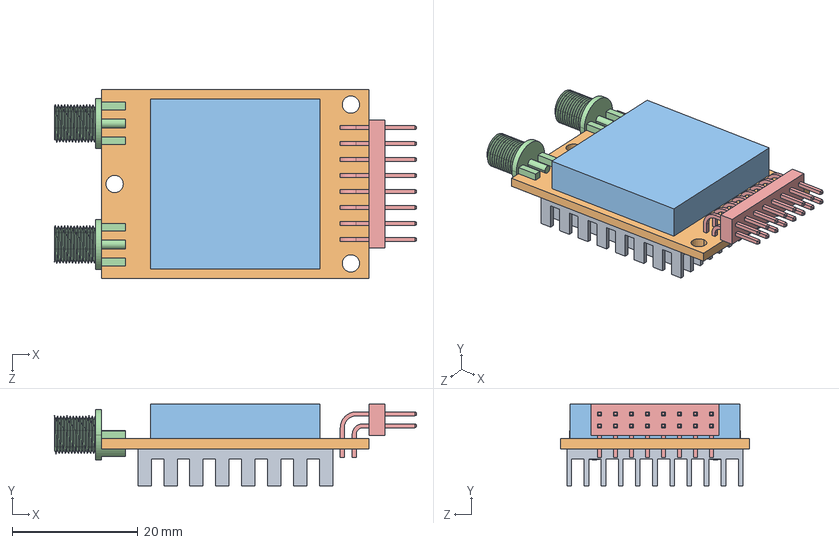
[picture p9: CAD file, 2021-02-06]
Hardware Design/CAD - Avionics Bay/BLTN-102-005 (SRAD Sled)/BLTN-102-005-003.SLDASM
57.6 x 13.0 x 30.0 mm
RFD900 Heat Sink.CATPart
RFD900 PCB.CATPart
RFD900 RF Shield.CATPart
RFD900 Antenna Header.CATPart x 2
RFD900 Header Pins.CATPart

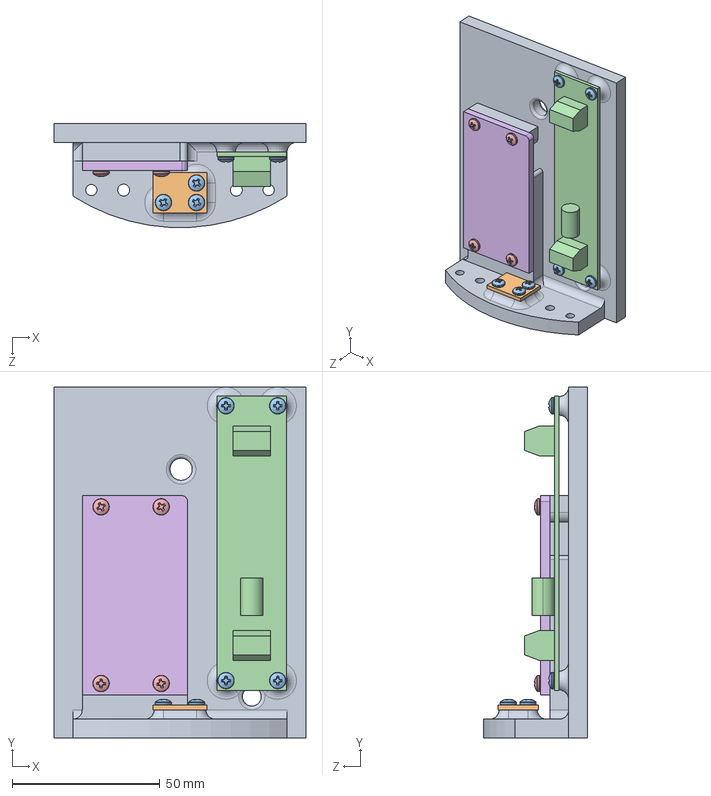
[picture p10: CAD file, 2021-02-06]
Hardware Design/CAD - Avionics Bay/BLTN-102-003 (RRC3 Card)/BLTN-102-003-000.SLDASM
85.1 x 118.6 x 35.1 mm
BLTN-102-003-001
BLTN-102-003-003
91249A108_BLACK-OXIDE FNSH PAN HEAD PHIL MACHINE SCREW x 7
BLTN-102-003-004
91249A115_BLACK-OXIDE FNSH PAN HEAD PHIL MACHINE SCREW x 4
BLTN-102-003-002
93365A120_HEAT-SET INSERTS FOR PLASTICS x 11

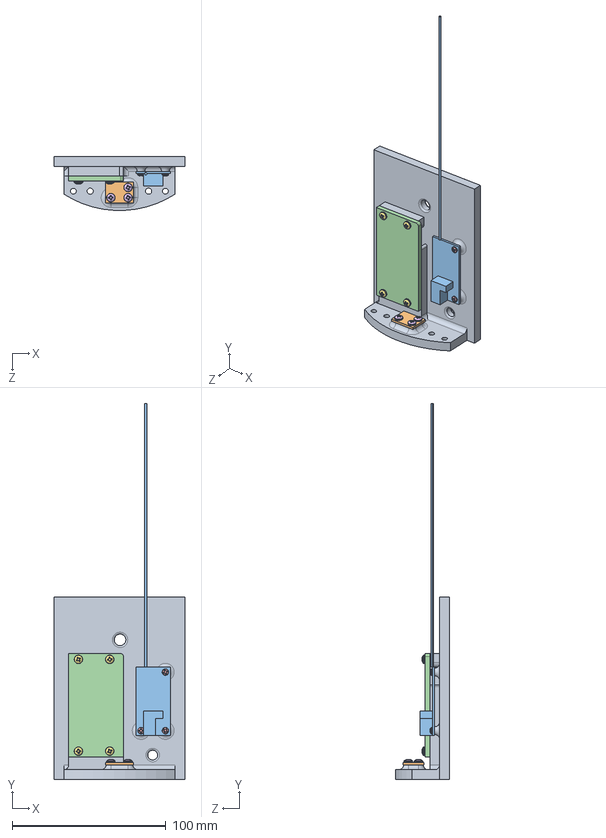
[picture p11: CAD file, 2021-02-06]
Hardware Design/CAD - Avionics Bay/BLTN-102-002 (BRB Card)/BLTN-102-002-000.SLDASM
85.1 x 244.5 x 34.9 mm
BLTN-102-002-001
BLTN-102-002-002
BLTN-102-002-003
BLTN-102-002-004
91249A054_BLACK-OXIDE FNSH PAN HEAD PHIL MACHINE SCREW x 3
91249A108_BLACK-OXIDE FNSH PAN HEAD PHIL MACHINE SCREW x 3
91249A115_BLACK-OXIDE FNSH PAN HEAD PHIL MACHINE SCREW x 4
93365A110_HEAT-SET INSERTS FOR PLASTICS x 3
93365A120_HEAT-SET INSERTS FOR PLASTICS x 7

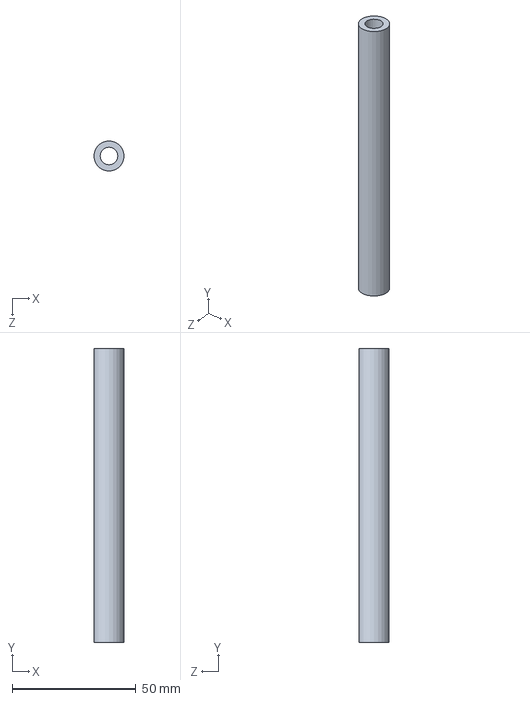
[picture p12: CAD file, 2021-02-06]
Hardware Design/CAD - Avionics Bay/BLTN-102-000-002.SLDPRT
12.2 x 118.6 x 12.2 mm

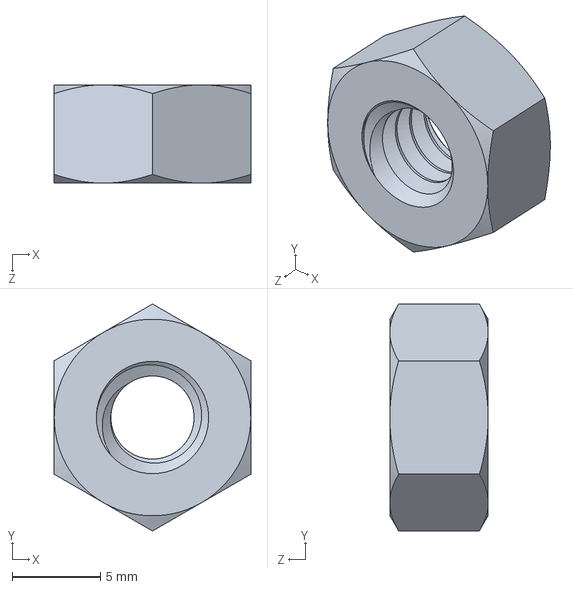
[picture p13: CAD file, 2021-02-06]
Hardware Design/CAD - Avionics Bay/BLTN-102-004 (Fwd Bulkhead)/BLTN-102-004-004.SLDPRT
11.1 x 12.8 x 5.56 mm

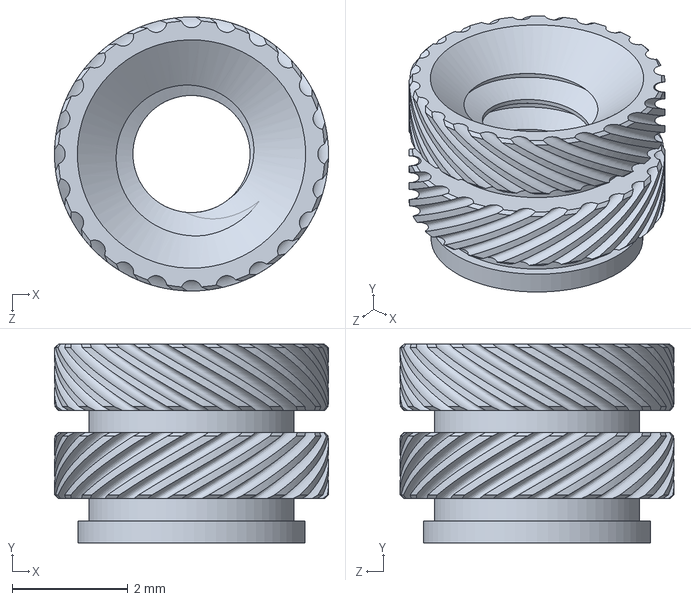
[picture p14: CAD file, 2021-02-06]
Hardware Design/CAD - Avionics Bay/BLTN-102-000-005.SLDPRT
4.72 x 3.43 x 4.72 mm

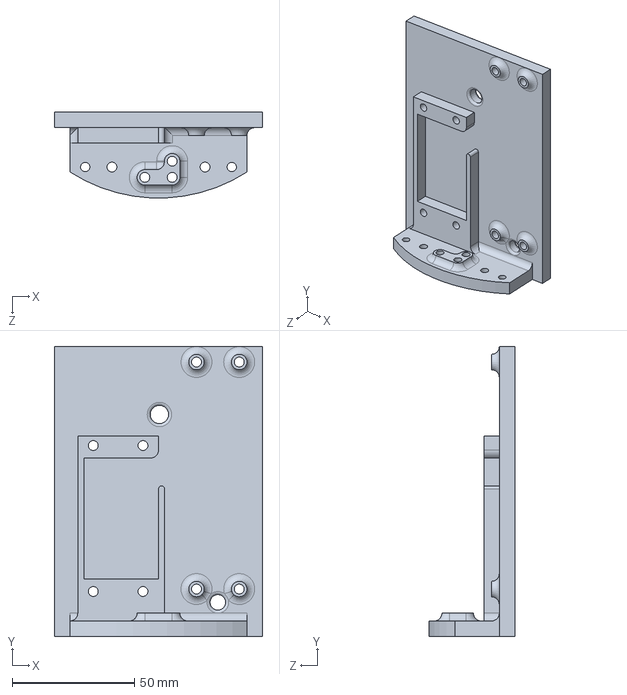
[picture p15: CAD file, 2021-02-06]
Hardware Design/CAD - Avionics Bay/BLTN-102-003 (RRC3 Card)/BLTN-102-003-001.SLDPRT
85.1 x 118.6 x 35.1 mm

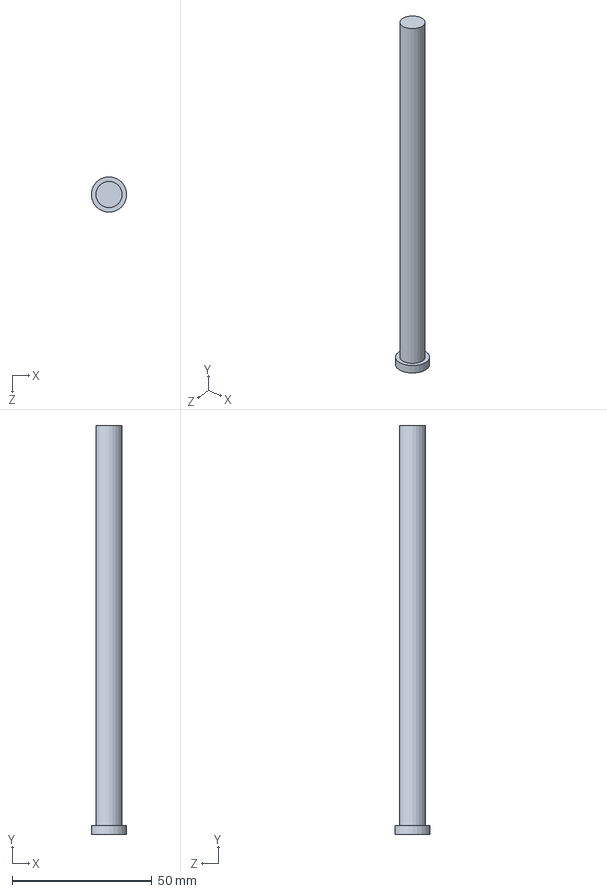
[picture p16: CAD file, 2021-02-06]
Hardware Design/CAD - Avionics Bay/BLTN-102-004 (Fwd Bulkhead)/BLTN-102-004-003.sldprt
12.7 x 146.4 x 12.7 mm

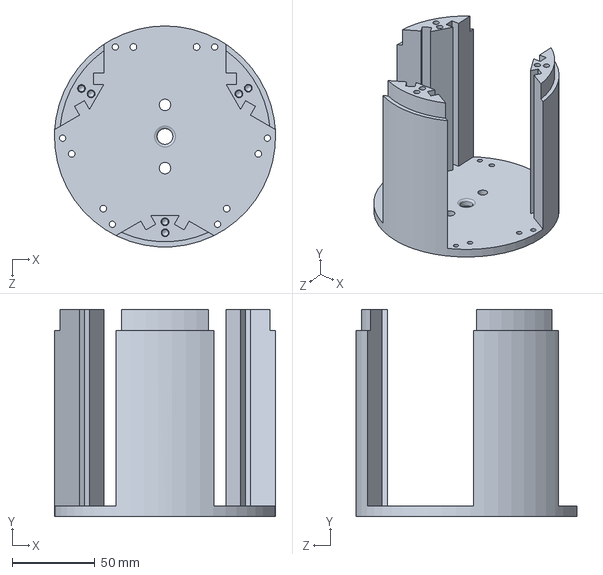
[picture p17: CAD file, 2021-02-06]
Hardware Design/CAD - Avionics Bay/BLTN-102-000-001.SLDPRT
133.3 x 125.0 x 133.4 mm

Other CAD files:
Hardware Design/CAD - Avionics Bay/BLTN-102-001 (Telemetrum Card)/BLTN-102-001-003.SLDPRT
Hardware Design/CAD - Avionics Bay/BLTN-102-003 (RRC3 Card)/BLTN-102-003-003.SLDPRT
Hardware Design/CAD - Avionics Bay/BLTN-102-006 (Wire Passthrough)/BLTN-102-006-001.SLDPRT
Hardware Design/CAD - Avionics Bay/BLTN-102-002 (BRB Card)/BLTN-102-002-001.SLDPRT
Hardware Design/CAD - Avionics Bay/90322A656_HIGH-STRENGTH STEEL THREADED ROD.SLDPRT
Hardware Design/CAD - Avionics Bay/90596A111.SLDPRT
Hardware Design/CAD - Avionics Bay/91249A111_BLACK-OXIDE FNSH PAN HEAD PHIL MACHINE SCREW.SLDPRT
Hardware Design/CAD - Avionics Bay/91772A108_18-8 SS PAN HEAD PHILLIPS MACHINE SCREW.SLDPRT
Hardware Design/CAD - Avionics Bay/93365A120.SLDPRT
Hardware Design/CAD - Avionics Bay/BLTN-102-000-003.SLDPRT
Hardware Design/CAD - Avionics Bay/BLTN-102-000-004.SLDPRT
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

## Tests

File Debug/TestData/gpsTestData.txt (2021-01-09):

$GPGGA,202410.000,4042.6000,N,07400.4858,W,1,4,3.14,276.7,M,-34.2,M,,*63
$GPRMC,202410.000,A,4042.6000,N,07400.4858,W,0.08,161.23,160412,,,A*70
$GPGGA,202411.000,4042.5999,N,07400.4854,W,1,3,17.31,275.8,M,-34.2,M,,*5D
$GPRMC,202411.000,A,4042.5999,N,07400.4854,W,0.14,161.23,160412,,,A*7A

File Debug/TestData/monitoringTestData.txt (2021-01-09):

7.1635 1 0 1 0 0 0
7.1634 1 0 1 0 1 0
7.1634 1 0 1 0 1 1
7.1634 1 0 1 0 0 1
7.1634 1 0 0 0 0 0
7.1630 1 0 1 0 0 0

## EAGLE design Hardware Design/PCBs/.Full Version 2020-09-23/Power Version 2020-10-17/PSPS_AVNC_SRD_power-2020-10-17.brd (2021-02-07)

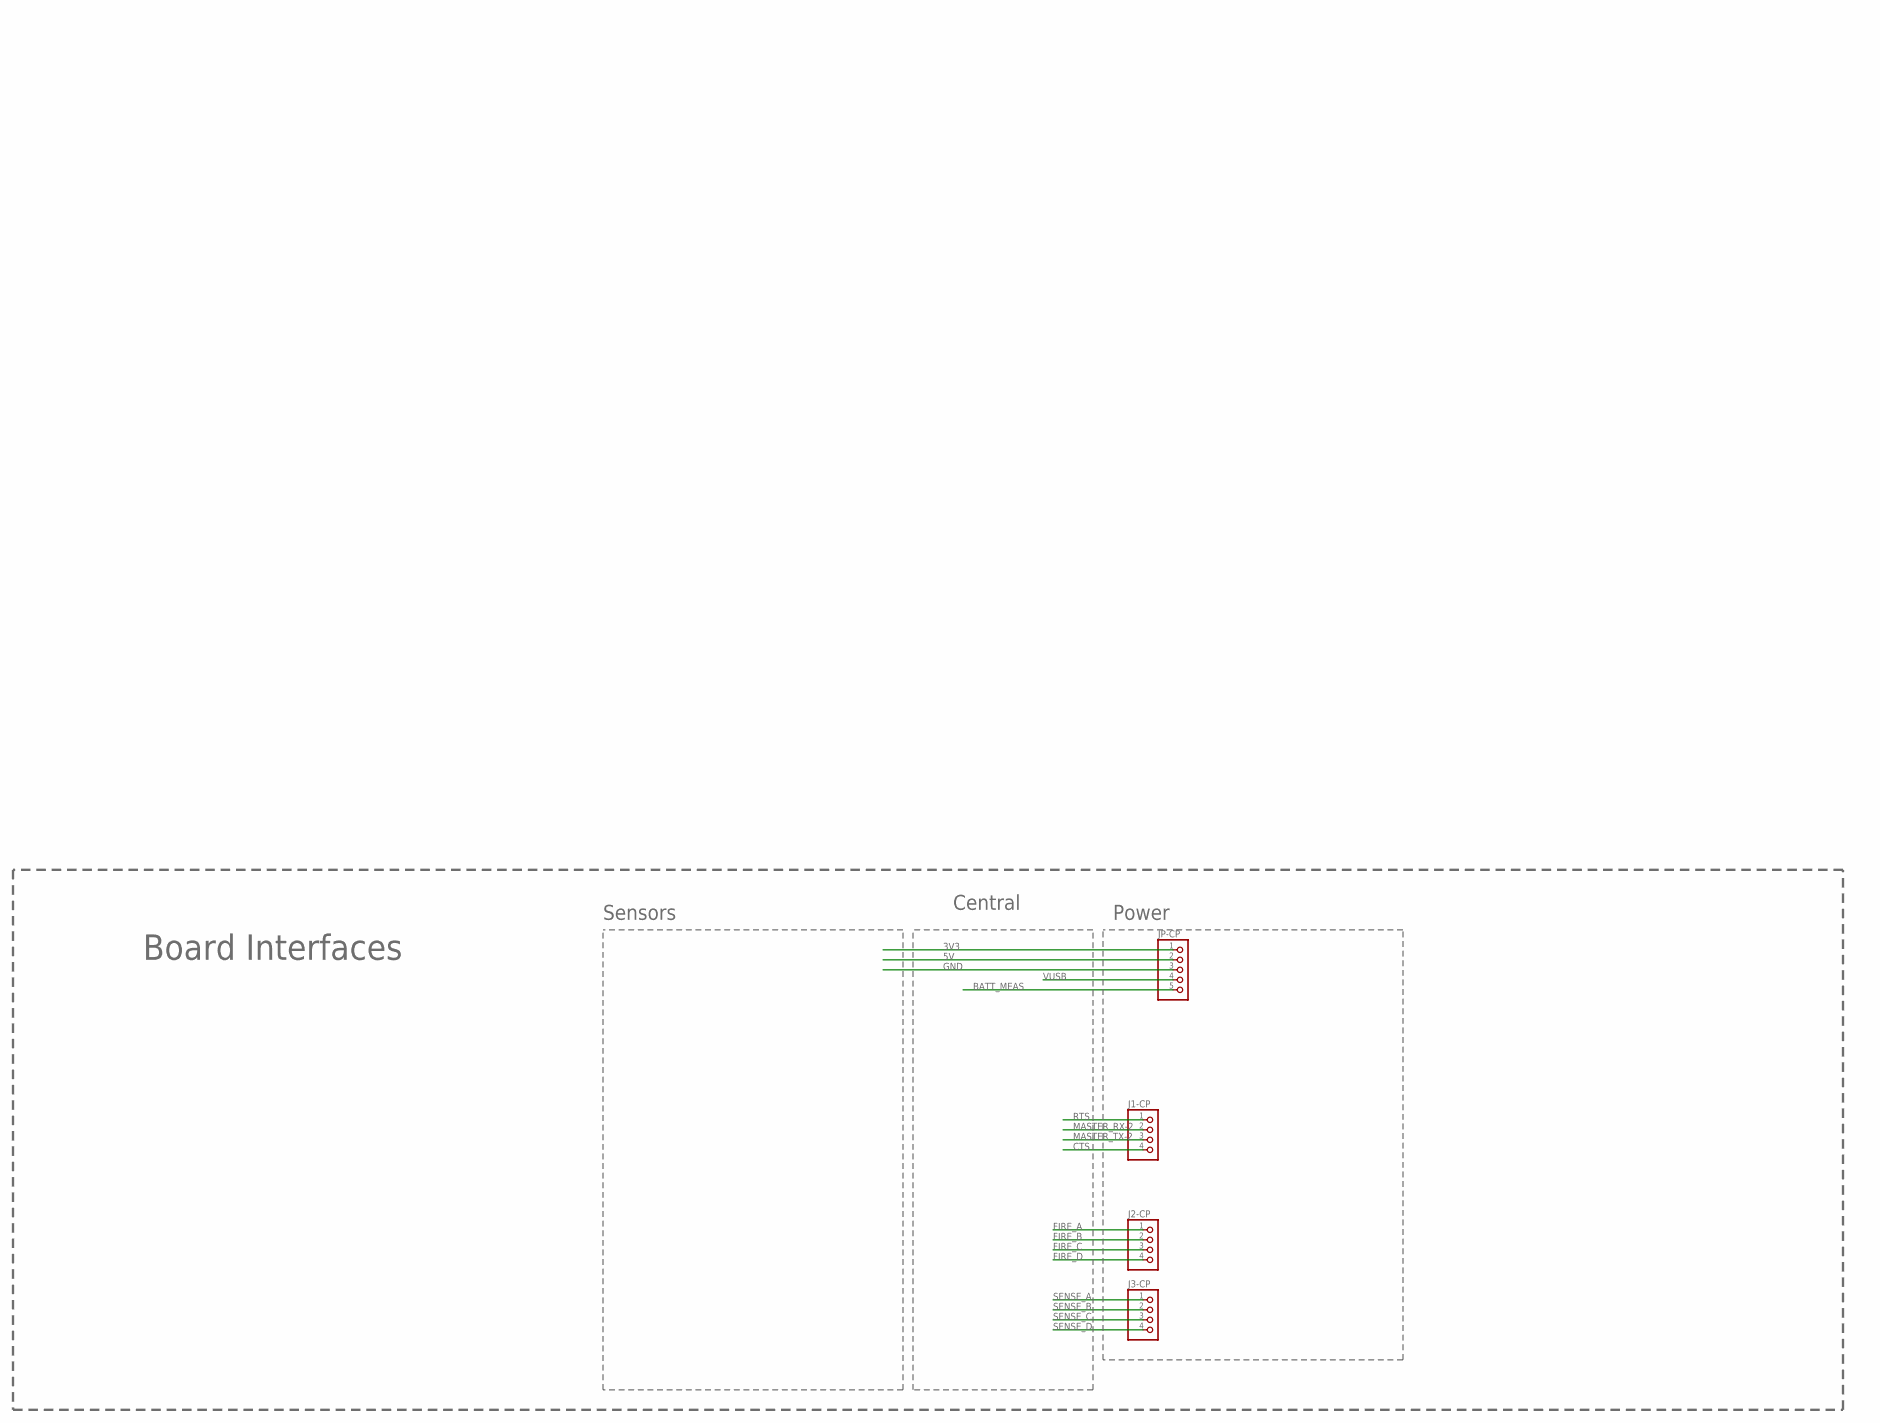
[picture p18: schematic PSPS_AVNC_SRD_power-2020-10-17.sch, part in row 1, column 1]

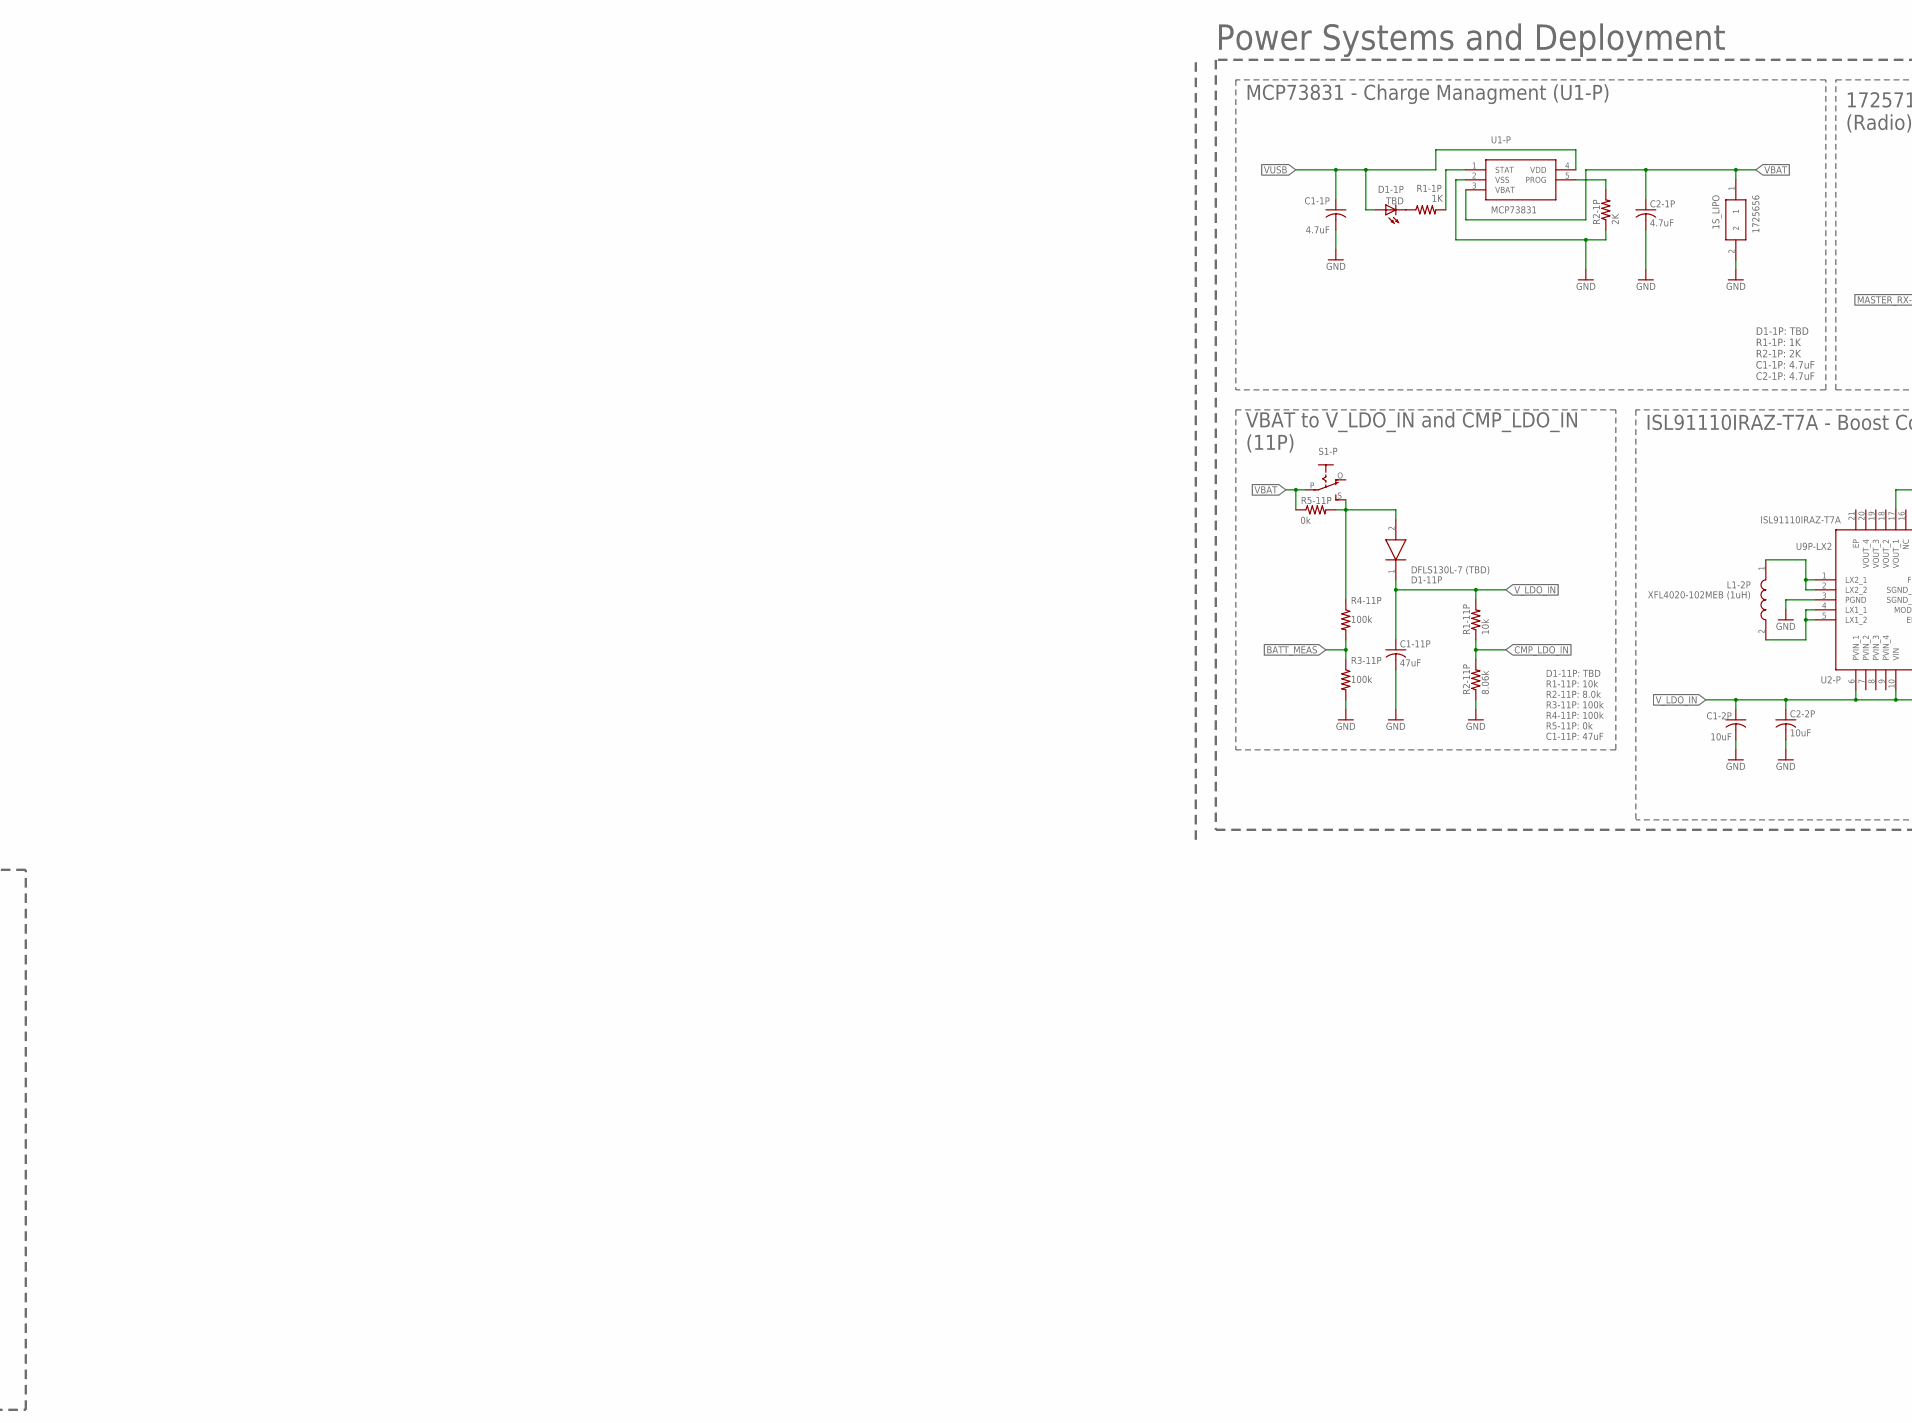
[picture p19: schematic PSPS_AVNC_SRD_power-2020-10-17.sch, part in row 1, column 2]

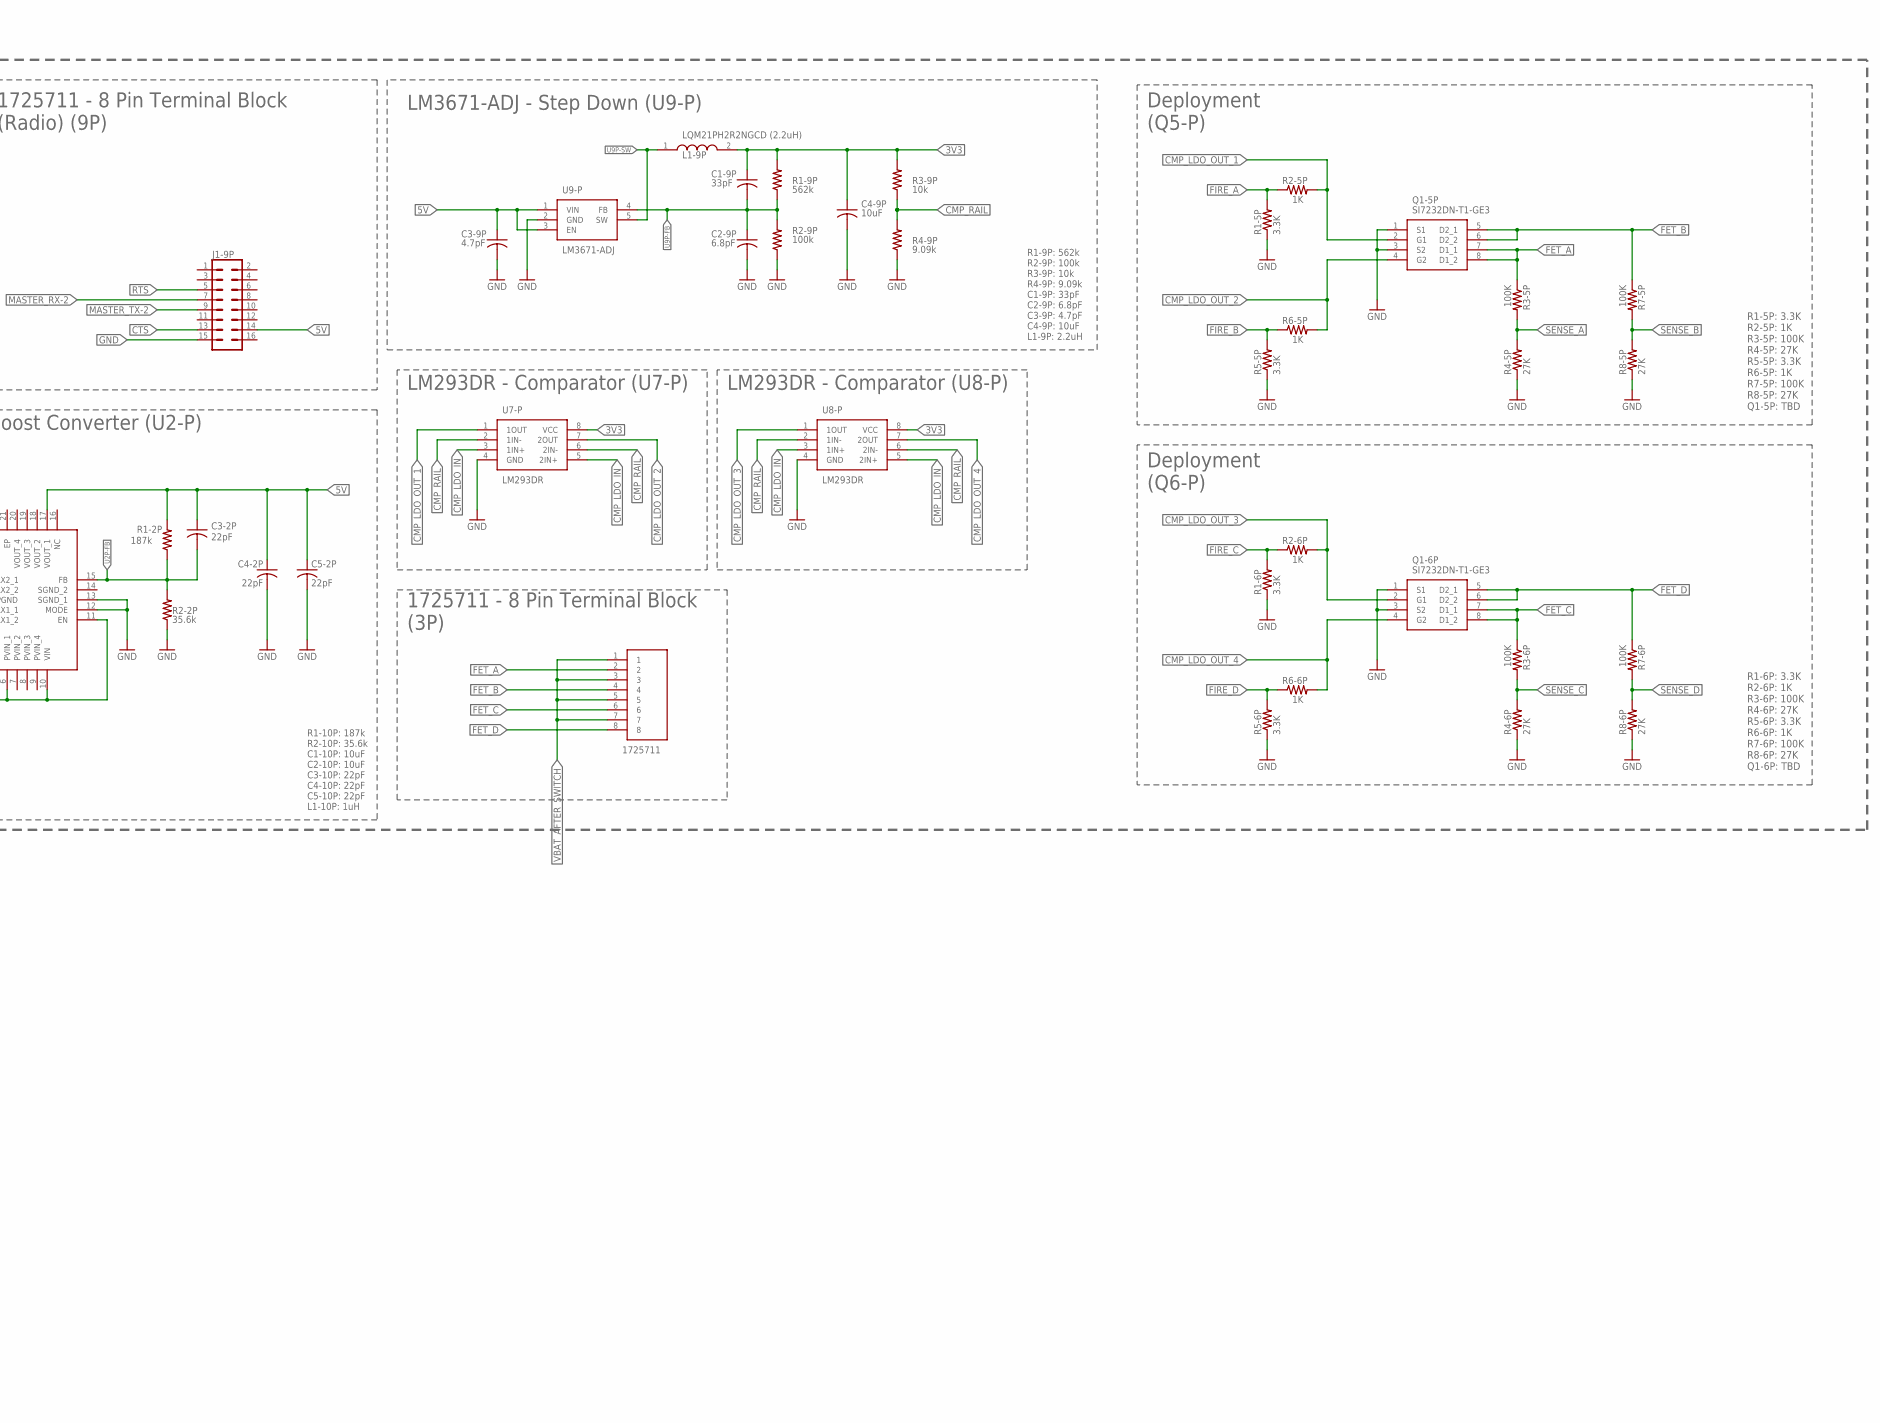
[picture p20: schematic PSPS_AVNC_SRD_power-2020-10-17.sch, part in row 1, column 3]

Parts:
1S_LIPO: 1725656
C1-1P, C2-1P: 4.7uF; C0805
C1-2P, C2-2P, C4-9P: 10uF; C0805
C1-9P: 33pF; C0805
C1-11P: 47uF; C0805
C2-9P: 6.8pF; C0805
C3-2P, C4-2P, C5-2P: 22pF; C0805
C3-9P: 4.7pF; C0805
D1-1P: TBD; CHIPLED_0805
D1-11P: DFLS130L-7 (TBD); POWERDI_123
J1-9P: CONN_08X2; 2X8
J1-CP, J2-CP, J3-CP: PINHD-1X4; 1X04
J2-P: 1725711
JP-CP: PINHD-1X5; 1X05
L1-2P: XFL4020-102MEB (1uH); XFL4020
L1-9P: LQM21PH2R2NGCD (2.2uH); INDC2012X100N
Q1-5P, Q1-6P: SI7232DN-T1-GE3; POWERPAK-1212-8
R1-1P: 1K; R0805
R1-2P: 187k; R0805
R1-5P, R1-6P, R5-5P, R5-6P: 3.3K; M0805
R1-9P: 562k; R0805
R1-11P, R3-9P: 10k; R0805
R2-1P: 2K; R0805
R2-2P: 35.6k; R0805
R2-5P, R2-6P, R6-5P, R6-6P: 1K; M0805
R2-9P, R3-11P, R4-11P: 100k; R0805
R2-11P: 8.06k; R0805
R3-5P, R3-6P, R7-5P, R7-6P: 100K; M0805
R4-5P, R4-6P, R8-5P, R8-6P: 27K; M0805
R4-9P: 9.09k; R0805
R5-11P: 0k; R0805
S1-P: EG1218S; EG1218
U1-P: MCP73831; SOT95P270X145-5N
U2-P: ISL91110IRAZ-T7A; QFN50P400X400X100-21N
U7-P, U8-P: LM293DR; SOIC127P600X175-8N
U9-P: LM3671-ADJ; SOT95P280X145-5N

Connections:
3V3: C1-9P.1, C4-9P.1, JP-CP.1, L1-9P.2, R1-9P.2, R3-9P.2, U7-P.8 (VCC), U8-P.8 (VCC)
5V: C3-2P.1, C3-9P.1, C4-2P.1, C5-2P.1, J1-9P.14, JP-CP.2, R1-2P.2, U2-P.17 (VOUT_1), U9-P.1 (VIN), U9-P.3 (EN)
BATT_MEAS: JP-CP.5, R3-11P.1, R4-11P.2
CMP_LDO_IN: R1-11P.1, R2-11P.2, U7-P.3 (1IN+), U7-P.5 (2IN+), U8-P.3 (1IN+), U8-P.5 (2IN+)
CMP_LDO_OUT_1: Q1-5P.2 (G1), R2-5P.2, U7-P.1 (1OUT)
CMP_LDO_OUT_2: Q1-5P.4 (G2), R6-5P.2, U7-P.7 (2OUT)
CMP_LDO_OUT_3: Q1-6P.2 (G1), R2-6P.2, U8-P.1 (1OUT)
CMP_LDO_OUT_4: Q1-6P.4 (G2), R6-6P.2, U8-P.7 (2OUT)
CMP_RAIL: R3-9P.1, R4-9P.2, U7-P.2 (1IN-), U7-P.6 (2IN-), U8-P.2 (1IN-), U8-P.6 (2IN-)
CTS: J1-9P.13, J1-CP.4
D1-1P_R1-1P: D1-1P.C, R1-1P.1
FET_A: J2-P.2, Q1-5P.7 (D1_1), Q1-5P.8 (D1_2), R3-5P.1
FET_B: J2-P.4, Q1-5P.5 (D2_1), Q1-5P.6 (D2_2), R7-5P.1
FET_C: J2-P.6, Q1-6P.7 (D1_1), Q1-6P.8 (D1_2), R3-6P.1
FET_D: J2-P.8, Q1-6P.5 (D2_1), Q1-6P.6 (D2_2), R7-6P.1
FIRE_A: J2-CP.1, R1-5P.2, R2-5P.1
FIRE_B: J2-CP.2, R5-5P.2, R6-5P.1
FIRE_C: J2-CP.3, R1-6P.2, R2-6P.1
FIRE_D: J2-CP.4, R5-6P.2, R6-6P.1
GND: 1S_LIPO.2, C1-1P.2, C1-2P.2, C1-11P.2, C2-1P.2, C2-2P.2, C2-9P.2, C3-9P.2, C4-2P.2, C4-9P.2, C5-2P.2, J1-9P.15, JP-CP.3, Q1-5P.1 (S1), Q1-5P.3 (S2), Q1-6P.1 (S1), Q1-6P.3 (S2), R1-5P.1, R1-6P.1, R2-1P.1, R2-2P.1, R2-9P.1, R2-11P.1, R3-11P.2, R4-5P.1, R4-6P.1, R4-9P.1, R5-5P.1, R5-6P.1, R8-5P.1, R8-6P.1, U1-P.2 (VSS), U2-P.3 (PGND), U2-P.12 (MODE), U2-P.13 (SGND_1), U7-P.4 (GND), U8-P.4 (GND), U9-P.2 (GND)
MASTER_RX-2: J1-9P.7, J1-CP.2
MASTER_TX-2: J1-9P.9, J1-CP.3
RTS: J1-9P.5, J1-CP.1
SENSE_A: J3-CP.1, R3-5P.2, R4-5P.2
SENSE_B: J3-CP.2, R7-5P.2, R8-5P.2
SENSE_C: J3-CP.3, R3-6P.2, R4-6P.2
SENSE_D: J3-CP.4, R7-6P.2, R8-6P.2
U1P-PROG: R2-1P.2, U1-P.5 (PROG)
U1P-STAT: R1-1P.2, U1-P.1 (STAT)
U2P-FB: C3-2P.2, R1-2P.1, R2-2P.2, U2-P.15 (FB)
U9P-FB: C1-9P.2, C2-9P.1, R1-9P.1, R2-9P.2, U9-P.4 (FB)
U9P-LX1: L1-2P.2, U2-P.4 (LX1_1), U2-P.5 (LX1_2)
U9P-LX2: L1-2P.1, U2-P.1 (LX2_1), U2-P.2 (LX2_2)
U9P-SW: L1-9P.1, U9-P.5 (SW)
VBAT: 1S_LIPO.1, C2-1P.1, R5-11P.1, S1-P.P, U1-P.3 (VBAT)
VBAT_AFTER_SWITCH: D1-11P.2 (A), J2-P.1, J2-P.3, J2-P.5, J2-P.7, R4-11P.1, R5-11P.2, S1-P.S
VUSB: C1-1P.1, D1-1P.A, JP-CP.4, U1-P.4 (VDD)
V_LDO_IN: C1-2P.1, C1-11P.1, C2-2P.1, D1-11P.1 (K), R1-11P.2, U2-P.6 (PVIN_1), U2-P.10 (VIN), U2-P.11 (EN)

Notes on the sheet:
Power Systems and Deployment
Deployment (Q5-P)
R1-5P: 3.3K R2-5P: 1K R3-5P: 100K R4-5P: 27K R5-5P: 3.3K R6-5P: 1K R7-5P: 100K R8-5P: 27K Q1-5P: TBD
1725711 - 8 Pin Terminal Block (3P)
MCP73831 - Charge Managment (U1-P)
D1-1P: TBD R1-1P: 1K R2-1P: 2K C1-1P: 4.7uF C2-1P: 4.7uF
LM3671-ADJ - Step Down (U9-P)
R1-9P: 562k R2-9P: 100k R3-9P: 10k R4-9P: 9.09k C1-9P: 33pF C2-9P: 6.8pF C3-9P: 4.7pF C4-9P: 10uF L1-9P: 2.2uH
LM293DR - Comparator (U7-P)
ISL91110IRAZ-T7A - Boost Converter (U2-P)
R1-10P: 187k R2-10P: 35.6k C1-10P: 10uF C2-10P: 10uF C3-10P: 22pF C4-10P: 22pF C5-10P: 22pF L1-10P: 1uH
VBAT to V_LDO_IN and CMP_LDO_IN (11P)
D1-11P: TBD R1-11P: 10k R2-11P: 8.0k R3-11P: 100k R4-11P: 100k R5-11P: 0k C1-11P: 47uF
Deployment (Q6-P)
R1-6P: 3.3K R2-6P: 1K R3-6P: 100K R4-6P: 27K R5-6P: 3.3K R6-6P: 1K R7-6P: 100K R8-6P: 27K Q1-6P: TBD
LM293DR - Comparator (U8-P)
1725711 - 8 Pin Terminal Block (Radio) (9P)
Central
Power
Sensors
Board Interfaces

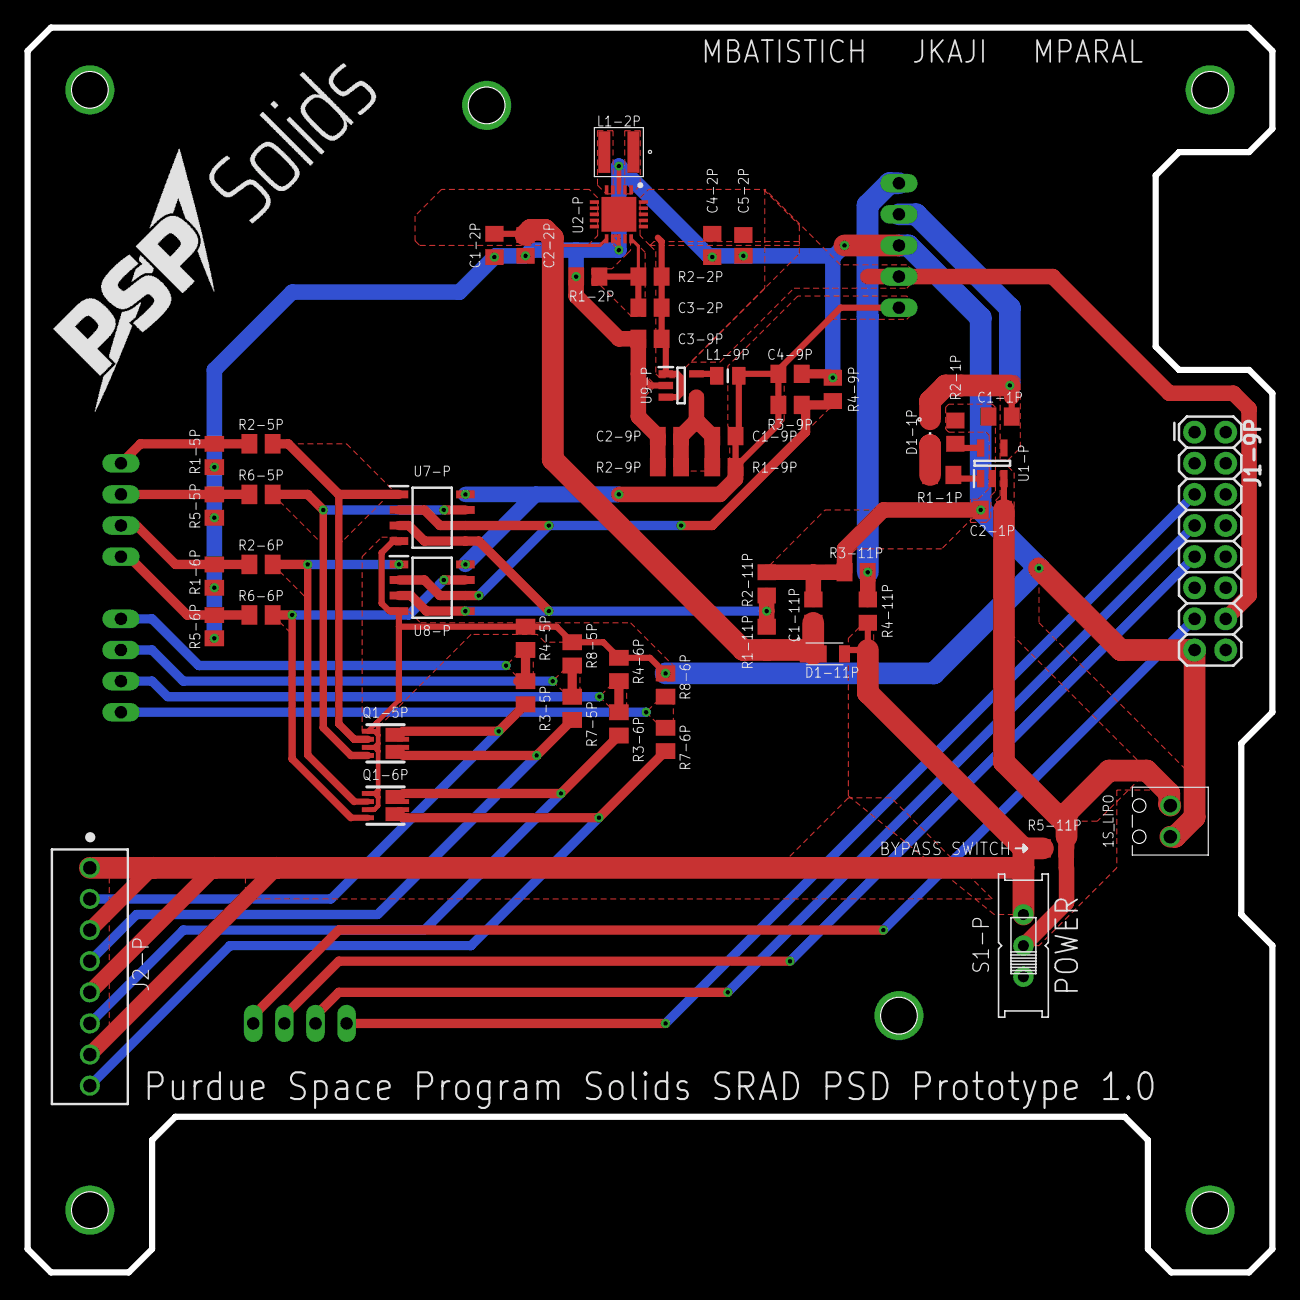
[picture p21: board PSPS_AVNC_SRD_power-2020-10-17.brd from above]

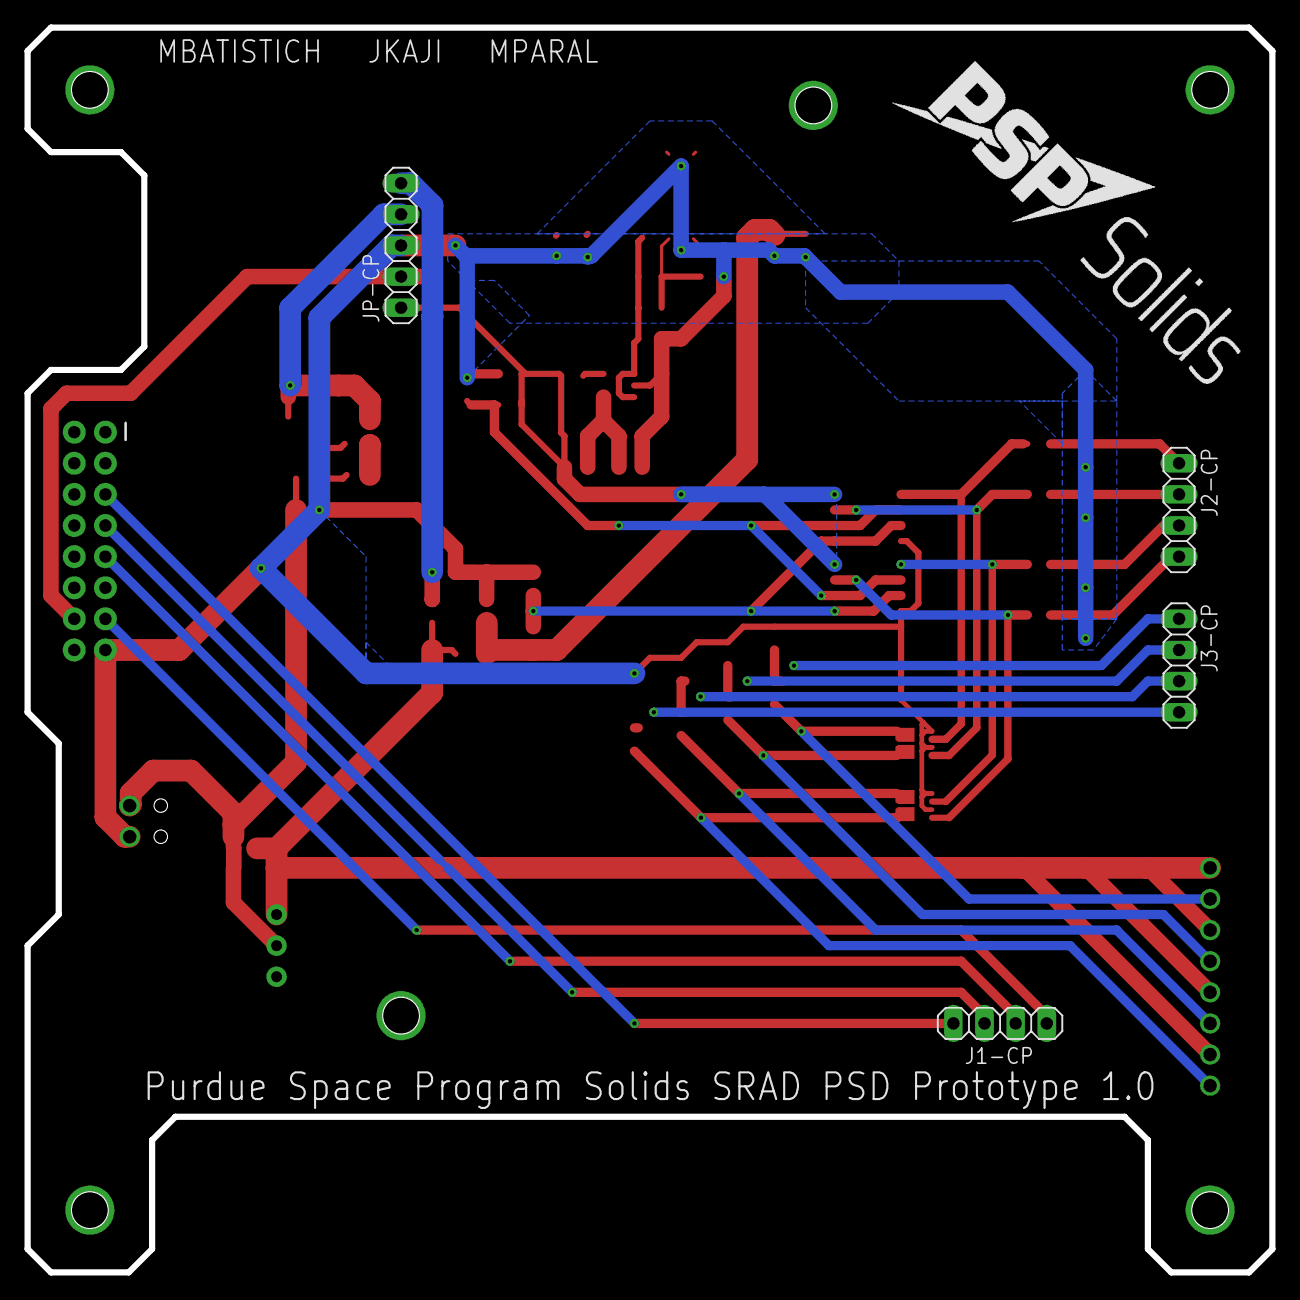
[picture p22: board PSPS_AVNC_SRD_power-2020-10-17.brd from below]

Board: 2 copper layers, 101.6 x 101.6 mm, 60 parts (4 on the bottom side), 38 nets.

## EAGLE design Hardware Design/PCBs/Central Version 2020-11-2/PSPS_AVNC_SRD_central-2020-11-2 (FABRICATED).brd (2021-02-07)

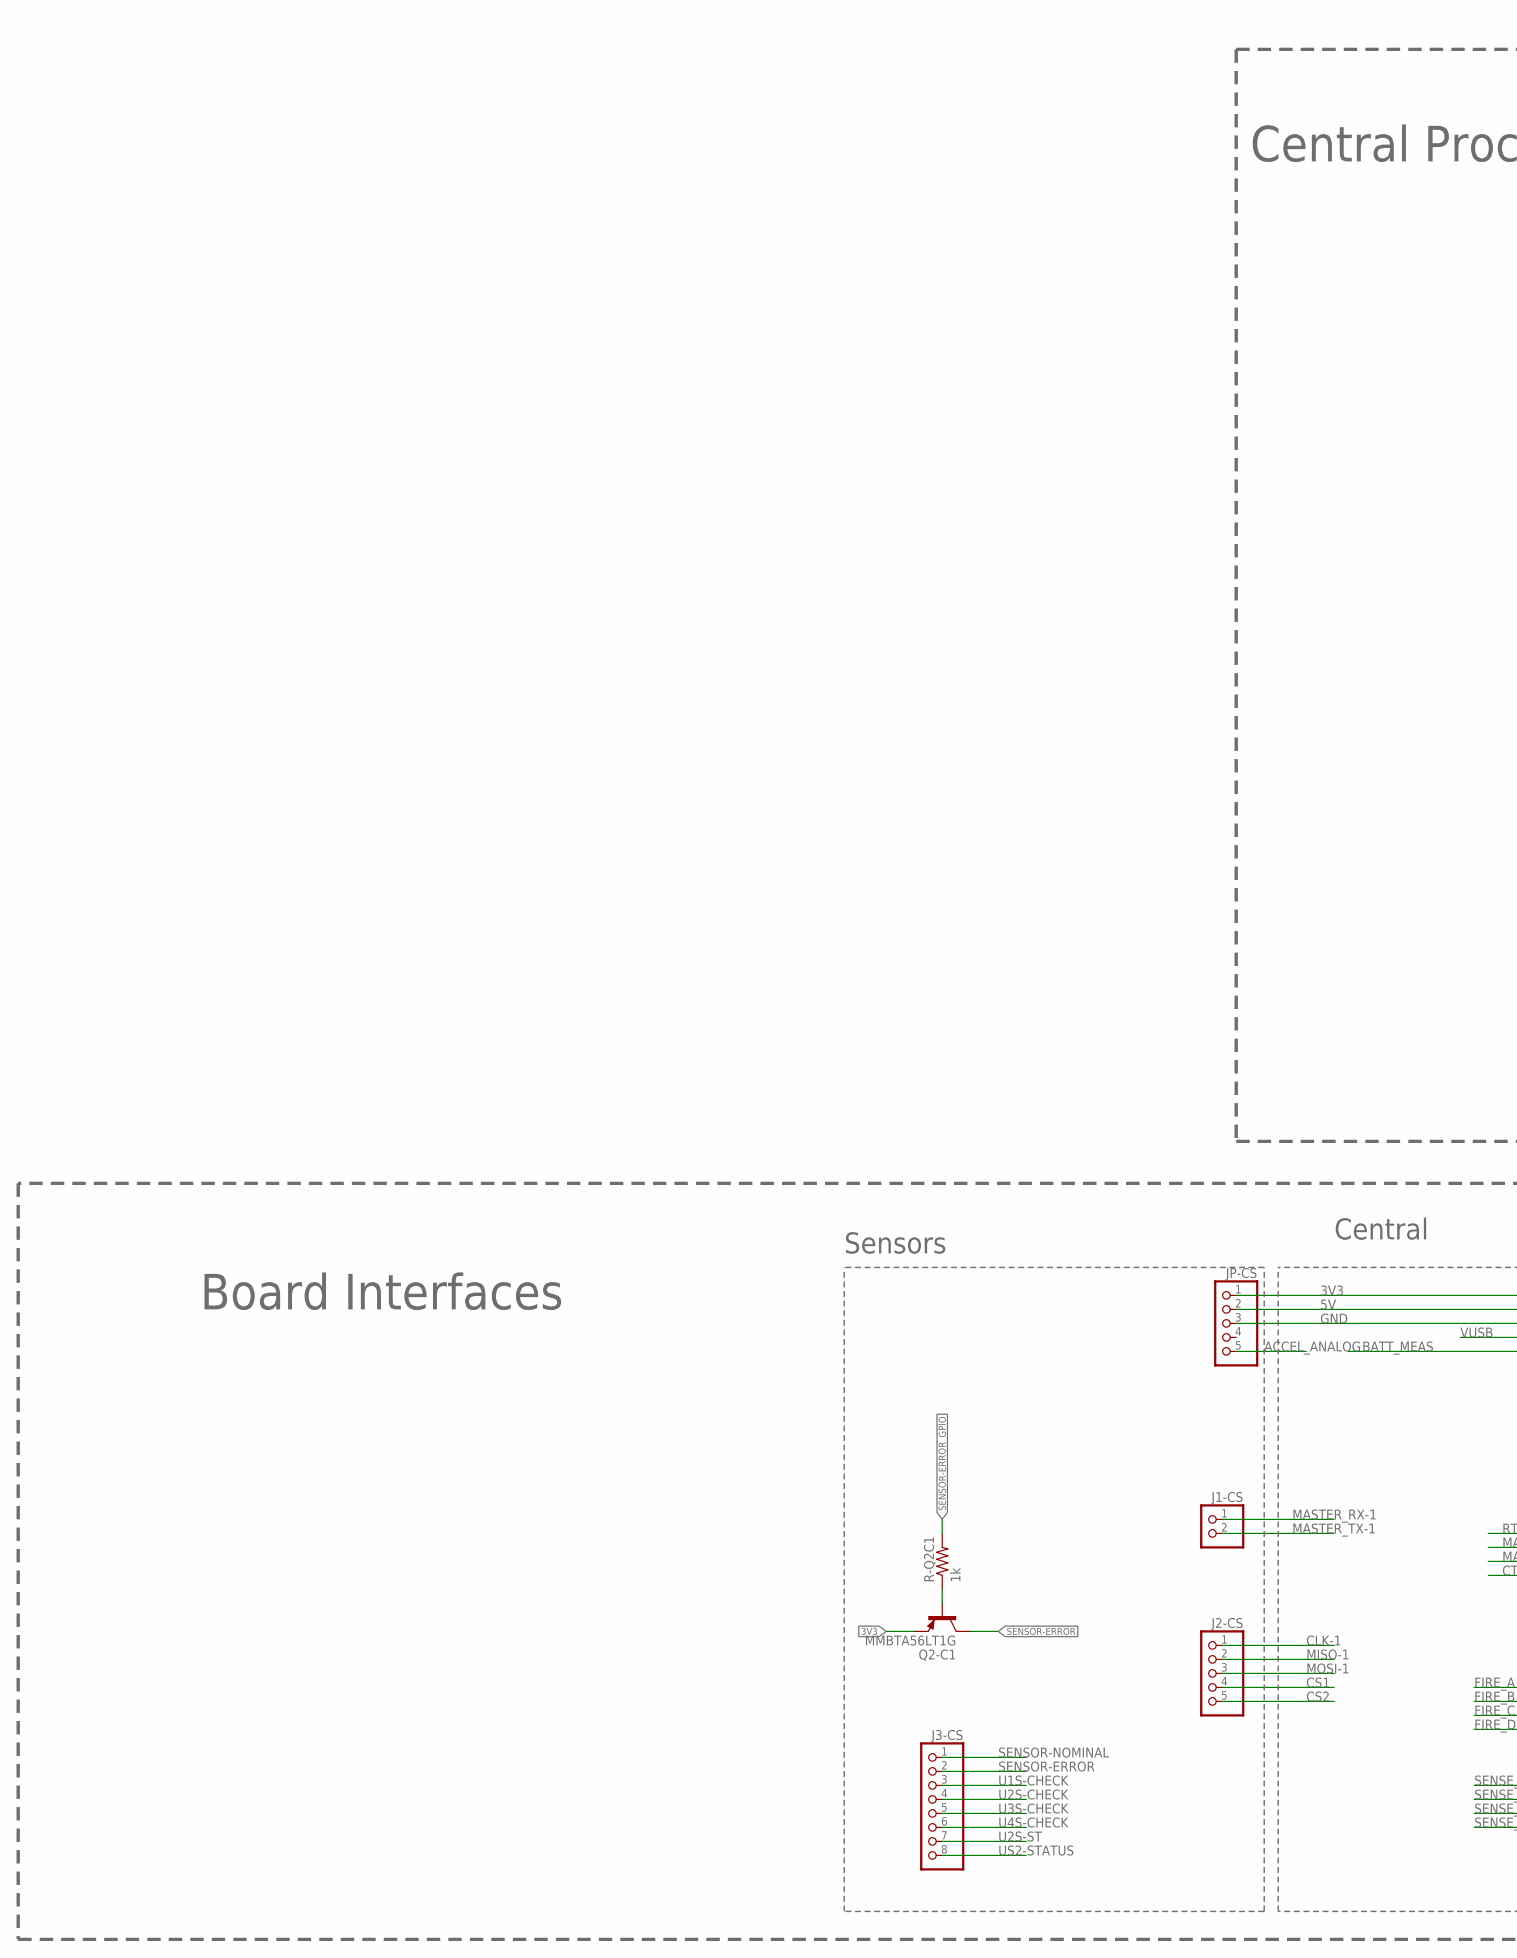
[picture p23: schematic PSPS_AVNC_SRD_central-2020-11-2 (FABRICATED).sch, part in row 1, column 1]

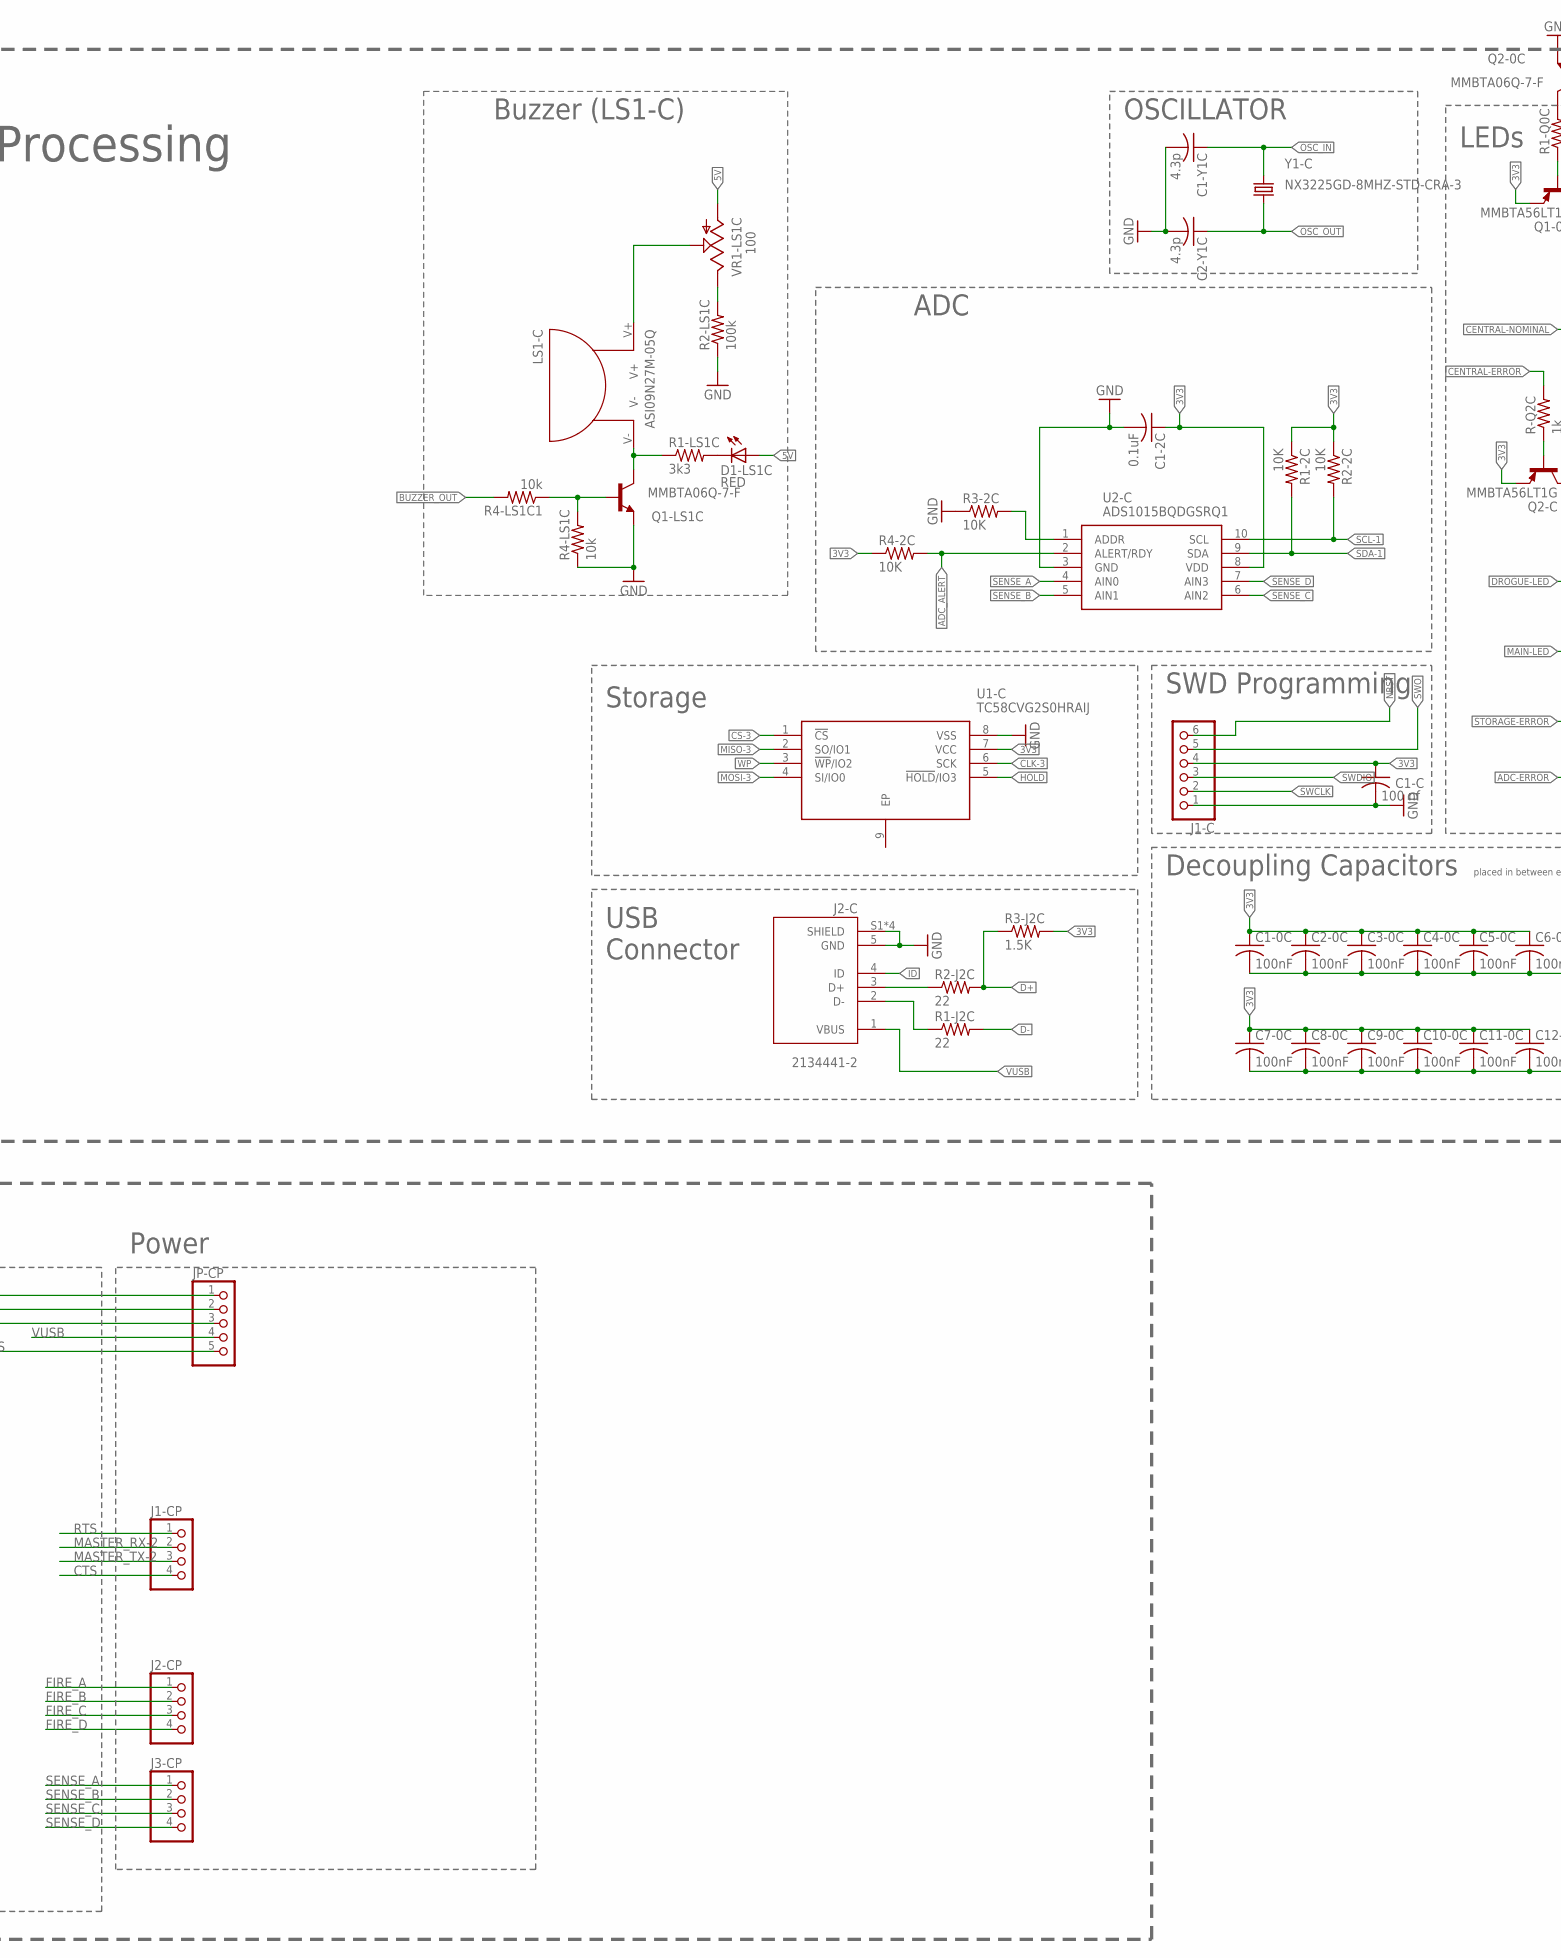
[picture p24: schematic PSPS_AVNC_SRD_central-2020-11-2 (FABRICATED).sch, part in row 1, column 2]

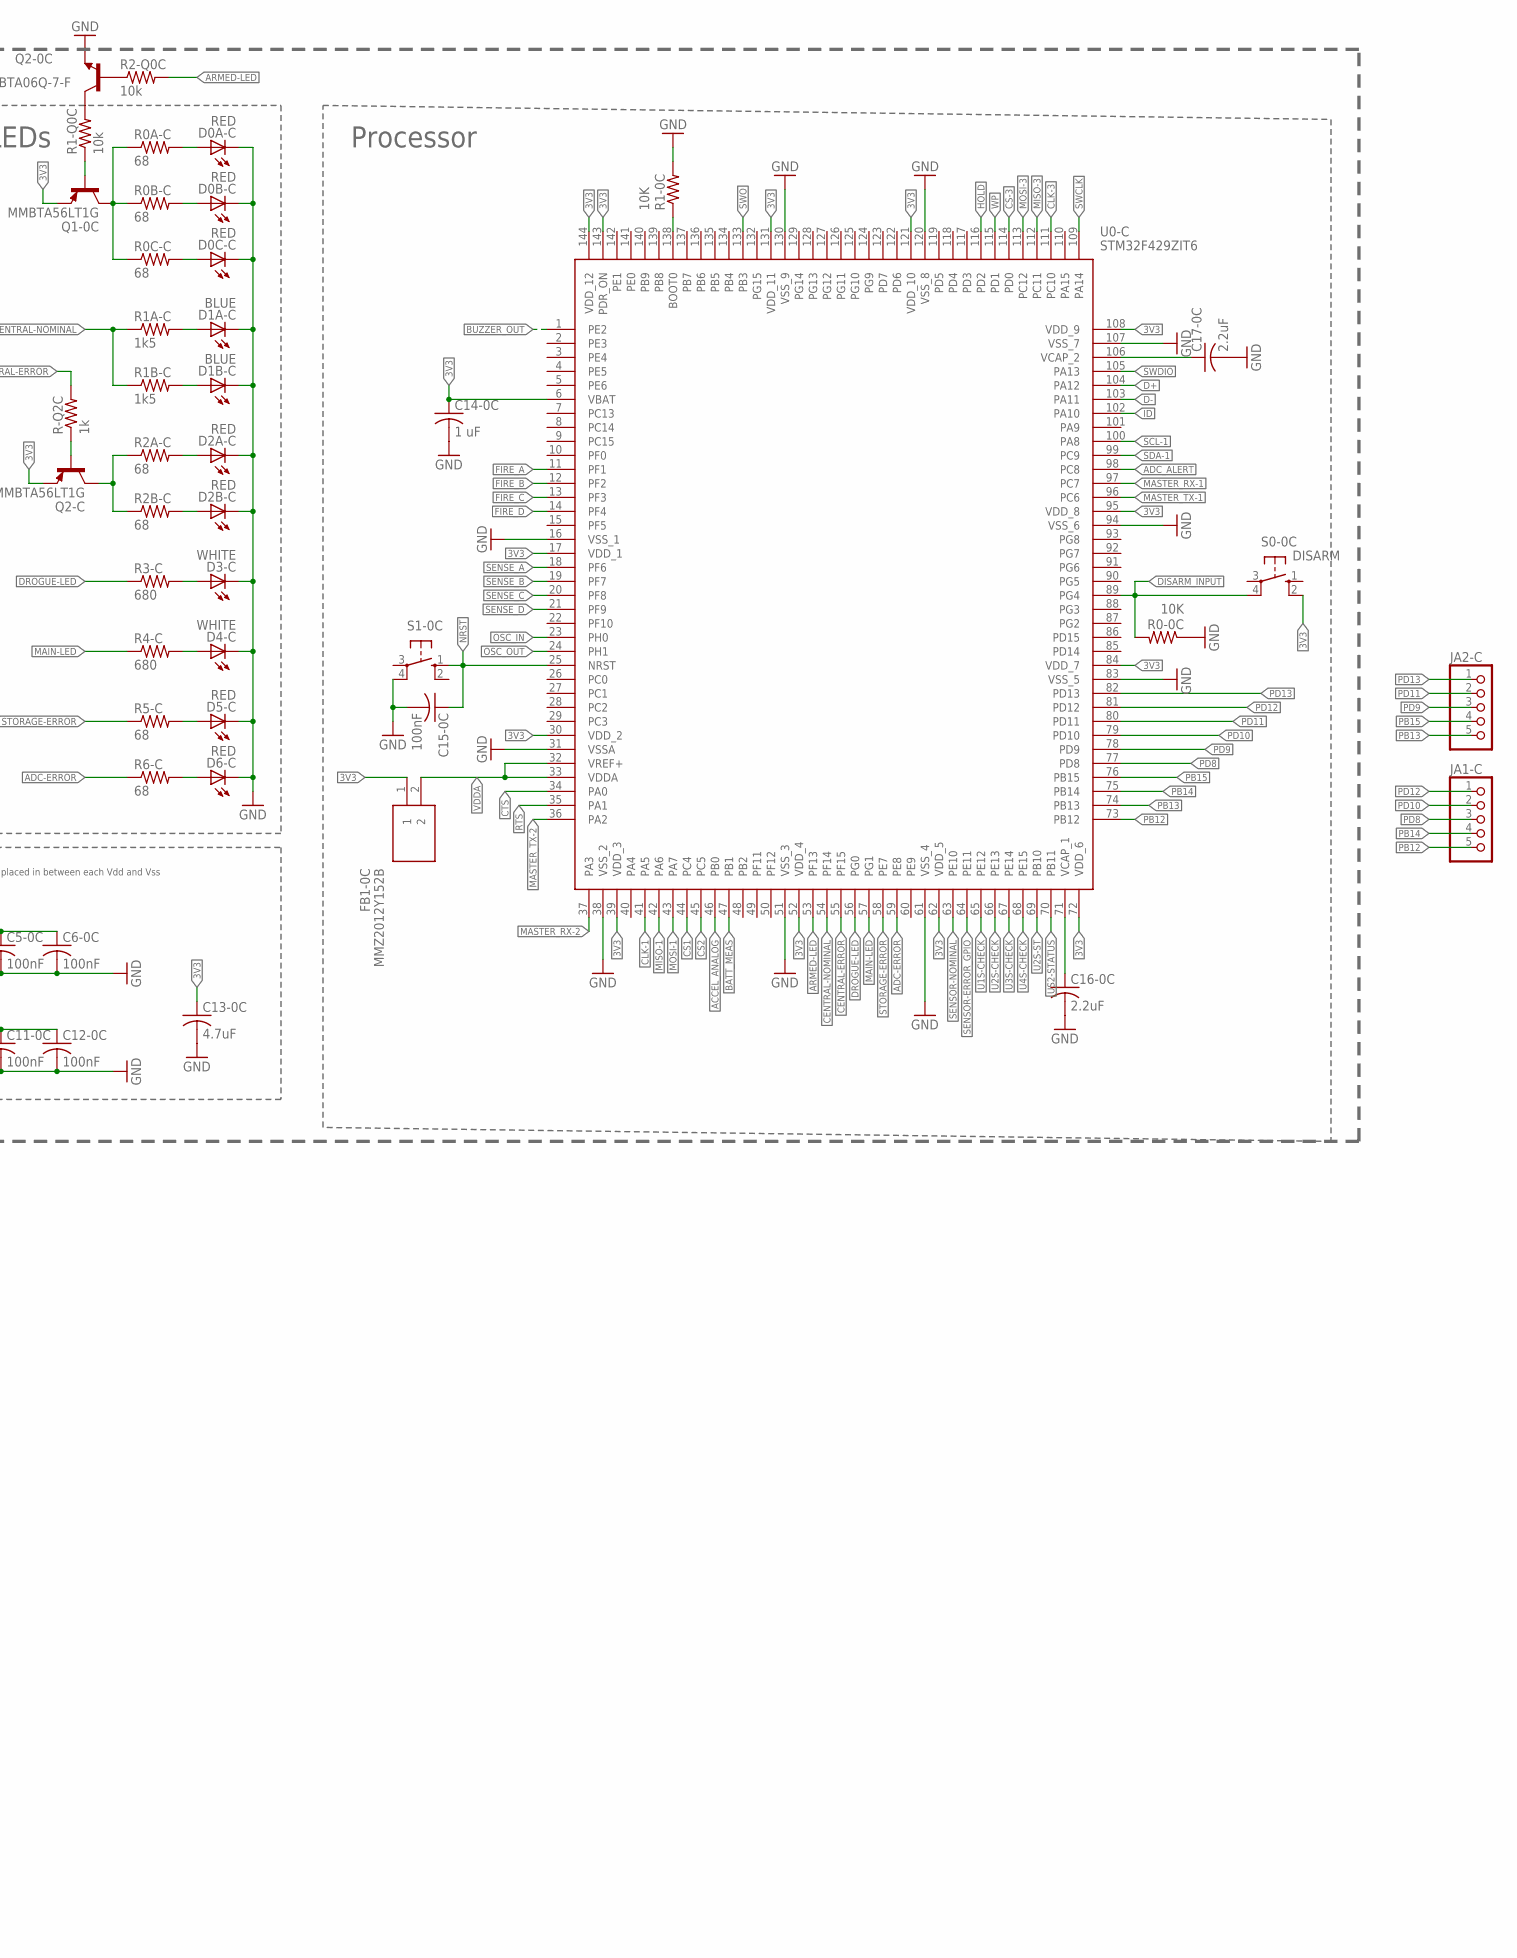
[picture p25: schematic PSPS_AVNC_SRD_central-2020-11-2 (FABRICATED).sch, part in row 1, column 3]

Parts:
C1-0C, C2-0C, C3-0C, C4-0C, C5-0C, C6-0C, C7-0C, C8-0C, C9-0C, C10-0C, C11-0C, C12-0C, C15-0C: 100nF; C0805
C1-2C: 0.1uF; C0805
C1-C: 100 nf; C0805
C1-Y1C, C2-Y1C: 4.3p; C0805
C13-0C: 4.7uF; C0805
C14-0C: 1 uF; C0805
C16-0C, C17-0C: 2.2uF; C0805
D0A-C, D0B-C, D0C-C, D1-LS1C, D2A-C, D2B-C, D5-C, D6-C: RED; CHIPLED_0805
D1A-C, D1B-C: BLUE; CHIPLED_0805
D3-C, D4-C: WHITE; CHIPLED_0805
FB1-0C: MMZ2012Y152B; BEADC2012X105N
J1-C: PINHD-1X6; 1X06
J1-CP, J2-CP, J3-CP: PINHD-1X4; 1X04
J1-CS: PINHD-1X2; 1X02
J2-C: 2134441-2; TE_2134441-2
J2-CS: PINHD-1X5; 1X05
J3-CS: PINHD-1X8; 1X08
JA1-C, JA2-C: PINHD-1X5; 1X05
JP-CP: PINHD-1X5; 1X05
JP-CS: PINHD-1X5; 1X05
LS1-C: ASI09N27M-05Q
Q1-0C, Q2-C, Q2-C1: MMBTA56LT1G; SOT23
Q1-LS1C, Q2-0C: MMBTA06Q-7-F; SOT23
R0-0C, R1-0C, R1-2C, R2-2C, R3-2C, R4-2C: 10K; R0805
R0A-C, R0B-C, R0C-C, R2A-C, R2B-C, R5-C, R6-C: 68; M0805
R1-J2C, R2-J2C: 22; M0805
R1-LS1C: 3k3; R0805
R1-Q0C, R2-Q0C: 10k; M0805
R1A-C, R1B-C: 1k5; M0805
R2-LS1C: 100k; R0805
R3-C, R4-C: 680; M0805
R3-J2C: 1.5K; M0805
R4-LS1C, R4-LS1C1: 10k; R0805
R-Q2C, R-Q2C1: 1k; M0805
S0-0C: DISARM; B3F-10XX
S1-0C: 10-XX; B3F-10XX
U0-C: STM32F429ZIT6; QFP50P2200X2200X160-144N
U1-C: TC58CVG2S0HRAIJ; SON127P800X600X80-9N
U2-C: ADS1015BQDGSRQ1; SOP50P490X110-10N
VR1-LS1C: 100; LI10
Y1-C: NX3225GD-8MHZ-STD-CRA-3; NX3225GD

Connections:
3V3: C1-0C.1, C1-2C.1, C1-C.1, C2-0C.1, C3-0C.1, C4-0C.1, C5-0C.1, C6-0C.1, C7-0C.1, C8-0C.1, C9-0C.1, C10-0C.1, C11-0C.1, C12-0C.1, C13-0C.1, C14-0C.1, FB1-0C.1, J1-C.4, JP-CP.1, JP-CS.1, Q1-0C.2 (E), Q2-C.2 (E), Q2-C1.2 (E), R1-2C.1, R2-2C.1, R3-J2C.2, R4-2C.1, S0-0C.2 (S1), U0-C.6 (VBAT), U0-C.17 (VDD_1), U0-C.30 (VDD_2), U0-C.39 (VDD_3), U0-C.52 (VDD_4), U0-C.62 (VDD_5), U0-C.72 (VDD_6), U0-C.84 (VDD_7), U0-C.95 (VDD_8), U0-C.108 (VDD_9), U0-C.121 (VDD_10), U0-C.131 (VDD_11), U0-C.143 (PDR_ON), U0-C.144 (VDD_12), U1-C.7 (VCC), U2-C.8 (VDD)
5V: D1-LS1C.A, JP-CP.2, JP-CS.2, VR1-LS1C.A
ACCEL_ANALOG: JP-CS.5, U0-C.46 (PB0)
ADC-ERROR: R6-C.1, U0-C.59 (PE8)
ADC_ALERT: R4-2C.2, U0-C.98 (PC8), U2-C.2 (ALERT/RDY)
ADDR: R3-2C.2, U2-C.1 (ADDR)
ARMED-LED: R2-Q0C.2, U0-C.53 (PF13)
BATT_MEAS: JP-CP.5, U0-C.47 (PB1)
BOOT0: R1-0C.1, U0-C.138 (BOOT0)
BUZZER_OUT: R4-LS1C1.2, U0-C.1 (PE2)
CENTRAL-ERROR: R-Q2C.2, U0-C.55 (PF15)
CENTRAL-NOMINAL: R1A-C.1, R1B-C.1, U0-C.54 (PF14)
CLK-1: J2-CS.1, U0-C.41 (PA5)
CLK-3: U0-C.111 (PC10), U1-C.6 (SCK)
CS1: J2-CS.4, U0-C.44 (PC4)
CS2: J2-CS.5, U0-C.45 (PC5)
CS-3: U0-C.114 (PD0), U1-C.1 (!CS)
CTS: J1-CP.4, U0-C.34 (PA0)
D1-LS1C_R1-LS1C: D1-LS1C.C, R1-LS1C.2
D+: R2-J2C.2, R3-J2C.1, U0-C.104 (PA12)
D+_R2-J1C: J2-C.3 (D+), R2-J2C.1
D-: R1-J2C.2, U0-C.103 (PA11)
D-_R1-J1C: J2-C.2 (D-), R1-J2C.1
DISARM_INPUT: R0-0C.2, S0-0C.4 (P1), U0-C.89 (PG4)
DROGUE-LED: R3-C.1, U0-C.56 (PG0)
FIRE_A: J2-CP.1, U0-C.11 (PF1)
FIRE_B: J2-CP.2, U0-C.12 (PF2)
FIRE_C: J2-CP.3, U0-C.13 (PF3)
FIRE_D: J2-CP.4, U0-C.14 (PF4)
GND: C1-0C.2, C1-2C.2, C1-C.2, C1-Y1C.2, C2-0C.2, C2-Y1C.2, C3-0C.2, C4-0C.2, C5-0C.2, C6-0C.2, C7-0C.2, C8-0C.2, C9-0C.2, C10-0C.2, C11-0C.2, C12-0C.2, C13-0C.2, C14-0C.2, C15-0C.2, C16-0C.2, C17-0C.2, D0A-C.C, D0B-C.C, D0C-C.C, D1A-C.C, D1B-C.C, D2A-C.C, D2B-C.C, D3-C.C, D4-C.C, D5-C.C, D6-C.C, J1-C.1, J2-C.5 (GND), J2-C.S1 (SHIELD), J2-C.S2 (SHIELD), J2-C.S3 (SHIELD), J2-C.S4 (SHIELD), JP-CP.3, JP-CS.3, Q1-LS1C.3 (E), Q2-0C.3 (E), R0-0C.1, R1-0C.2, R2-LS1C.1, R3-2C.1, R4-LS1C.1, S1-0C.4 (P1), U0-C.16 (VSS_1), U0-C.31 (VSSA), U0-C.38 (VSS_2), U0-C.51 (VSS_3), U0-C.61 (VSS_4), U0-C.83 (VSS_5), U0-C.94 (VSS_6), U0-C.107 (VSS_7), U0-C.120 (VSS_8), U0-C.130 (VSS_9), U1-C.8 (VSS), U2-C.3 (GND)
HOLD: U0-C.116 (PD2), U1-C.5 (!HOLD!/IO3)
ID: J2-C.4 (ID), U0-C.102 (PA10)
LS1-C_Q1-LS1C: LS1-C.V-, Q1-LS1C.2 (C), R1-LS1C.1
MAIN-LED: R4-C.1, U0-C.57 (PG1)
MASTER_RX-1: J1-CS.1, U0-C.97 (PC7)
MASTER_RX-2: J1-CP.2, U0-C.37 (PA3)
MASTER_TX-1: J1-CS.2, U0-C.96 (PC6)
MASTER_TX-2: J1-CP.3, U0-C.36 (PA2)
MISO-1: J2-CS.2, U0-C.42 (PA6)
MISO-3: U0-C.112 (PC11), U1-C.2 (SO/IO1)
MOSI-1: J2-CS.3, U0-C.43 (PA7)
MOSI-3: U0-C.113 (PC12), U1-C.4 (SI/IO0)
unnamed: Q2-C1.1 (B), R-Q2C1.1
NRST: C15-0C.1, J1-C.6, S1-0C.1 (S), U0-C.25 (NRST)
OSC_IN: C1-Y1C.1, U0-C.23 (PH0), Y1-C.P$2 (2)
OSC_OUT: C2-Y1C.1, U0-C.24 (PH1), Y1-C.P$1 (1)
PB12: JA1-C.5, U0-C.73 (PB12)
PB13: JA2-C.5, U0-C.74 (PB13)
PB14: JA1-C.4, U0-C.75 (PB14)
PB15: JA2-C.4, U0-C.76 (PB15)
PD8: JA1-C.3, U0-C.77 (PD8)
PD9: JA2-C.3, U0-C.78 (PD9)
PD10: JA1-C.2, U0-C.79 (PD10)
PD11: JA2-C.2, U0-C.80 (PD11)
PD12: JA1-C.1, U0-C.81 (PD12)
PD13: JA2-C.1, U0-C.82 (PD13)
Q0-C_R0-C: Q1-0C.3 (C), R0A-C.1, R0B-C.1, R0C-C.1
Q1-0C_R-1Q0C: Q1-0C.1 (B), R1-Q0C.1
Q2-C_R2-C: Q2-C.3 (C), R2A-C.1, R2B-C.1
R0A-C_D0A-C: D0A-C.A, R0A-C.2
R0B-C_D0B-C: D0B-C.A, R0B-C.2
R0C-C_D0C-C: D0C-C.A, R0C-C.2
R1-Q0C_Q2-0C: Q2-0C.2 (C), R1-Q0C.2
R1A-C_D1A-C: D1A-C.A, R1A-C.2
R1B-C_D1B-C: D1B-C.A, R1B-C.2
R2-LS1C_LS1C: LS1-C.V+, VR1-LS1C.S
R2-Q0C_Q2-0C: Q2-0C.1 (B), R2-Q0C.1
R2A-C_D2A-C: D2A-C.A, R2A-C.2
R2B-C_D2B-C: D2B-C.A, R2B-C.2
R3-C_D3-C: D3-C.A, R3-C.2
R3-LS1C_Q1-LS1C: Q1-LS1C.1 (B), R4-LS1C.2, R4-LS1C1.1
R4-C_D4-C: D4-C.A, R4-C.2
R5-C_D5-C: D5-C.A, R5-C.2
R6-C_D6-C: D6-C.A, R6-C.2
R-Q2C_Q2-C: Q2-C.1 (B), R-Q2C.1
RTS: J1-CP.1, U0-C.35 (PA1)
SCL-1: R2-2C.2, U0-C.100 (PA8), U2-C.10 (SCL)
SDA-1: R1-2C.2, U0-C.99 (PC9), U2-C.9 (SDA)
SENSE_A: J3-CP.1, U0-C.18 (PF6), U2-C.4 (AIN0)
SENSE_B: J3-CP.2, U0-C.19 (PF7), U2-C.5 (AIN1)
SENSE_C: J3-CP.3, U0-C.20 (PF8), U2-C.6 (AIN2)
SENSE_D: J3-CP.4, U0-C.21 (PF9), U2-C.7 (AIN3)
SENSOR-ERROR: J3-CS.2, Q2-C1.3 (C)
SENSOR-ERROR_GPIO: R-Q2C1.2, U0-C.64 (PE11)
SENSOR-NOMINAL: J3-CS.1, U0-C.63 (PE10)
STORAGE-ERROR: R5-C.1, U0-C.58 (PE7)
SWCLK: J1-C.2, U0-C.109 (PA14)
SWDIO: J1-C.3, U0-C.105 (PA13)
SWO: J1-C.5, U0-C.133 (PB3)
U1S-CHECK: J3-CS.3, U0-C.65 (PE12)
U2S-CHECK: J3-CS.4, U0-C.66 (PE13)
U2S-ST: J3-CS.7, U0-C.69 (PB10)
U3S-CHECK: J3-CS.5, U0-C.67 (PE14)
U4S-CHECK: J3-CS.6, U0-C.68 (PE15)
US2-STATUS: J3-CS.8, U0-C.70 (PB11)
VCAP_1: C16-0C.1, U0-C.71 (VCAP_1)
VCAP_2: C17-0C.1, U0-C.106 (VCAP_2)
VDDA: FB1-0C.2, U0-C.32 (VREF+), U0-C.33 (VDDA)
VR1-LS1C_R3-LS1C: R2-LS1C.2, VR1-LS1C.E
VUSB: J2-C.1 (VBUS), JP-CP.4
WP: U0-C.115 (PD1), U1-C.3 (!WP!/IO2)

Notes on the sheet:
Central Processing
placed in between each Vdd and Vss
Processor
Storage
Decoupling Capacitors
SWD Programming
LEDs
ADC
USB Connector
OSCILLATOR
Buzzer (LS1-C)
Central
Power
Sensors
Board Interfaces

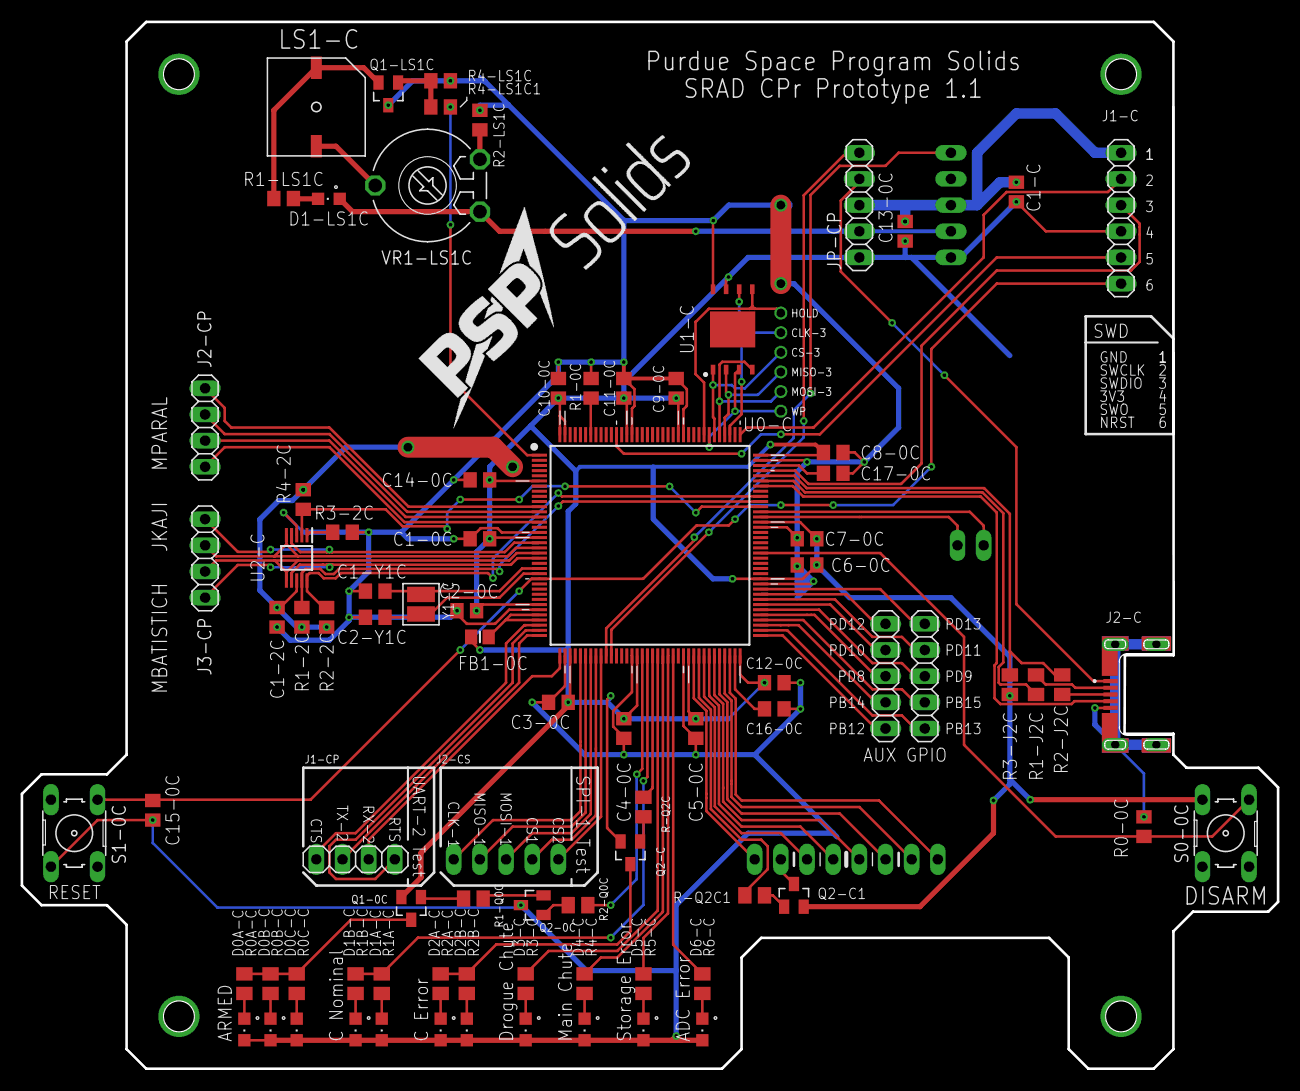
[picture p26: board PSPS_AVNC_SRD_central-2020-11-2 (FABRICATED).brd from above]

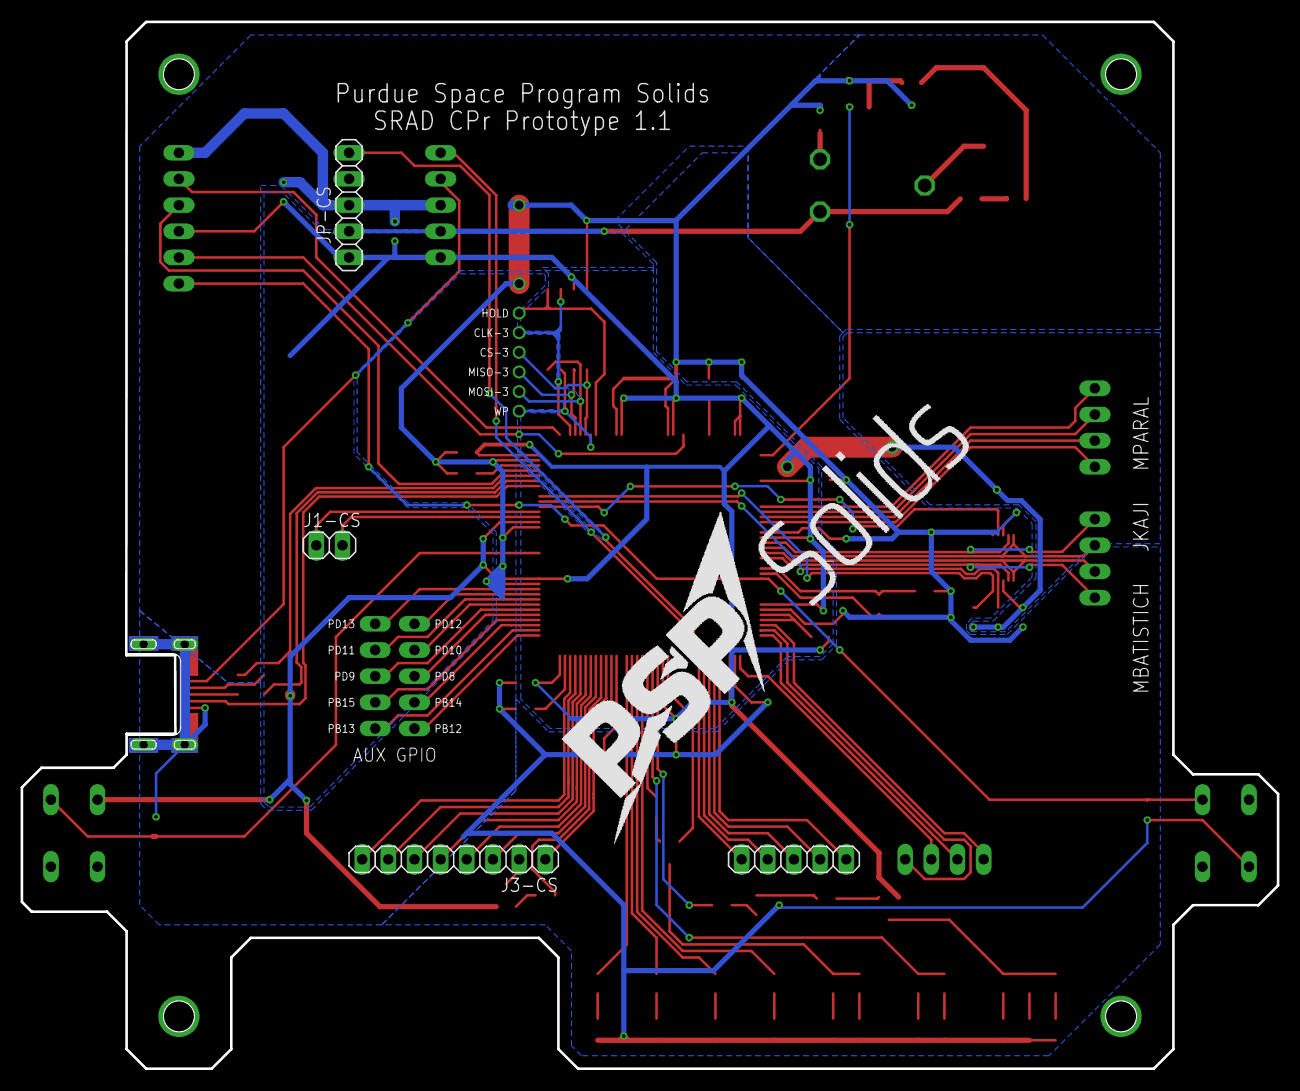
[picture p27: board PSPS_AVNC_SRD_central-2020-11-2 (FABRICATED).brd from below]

Board: 2 copper layers, 121.9 x 101.6 mm, 87 parts (4 on the bottom side), 101 nets.

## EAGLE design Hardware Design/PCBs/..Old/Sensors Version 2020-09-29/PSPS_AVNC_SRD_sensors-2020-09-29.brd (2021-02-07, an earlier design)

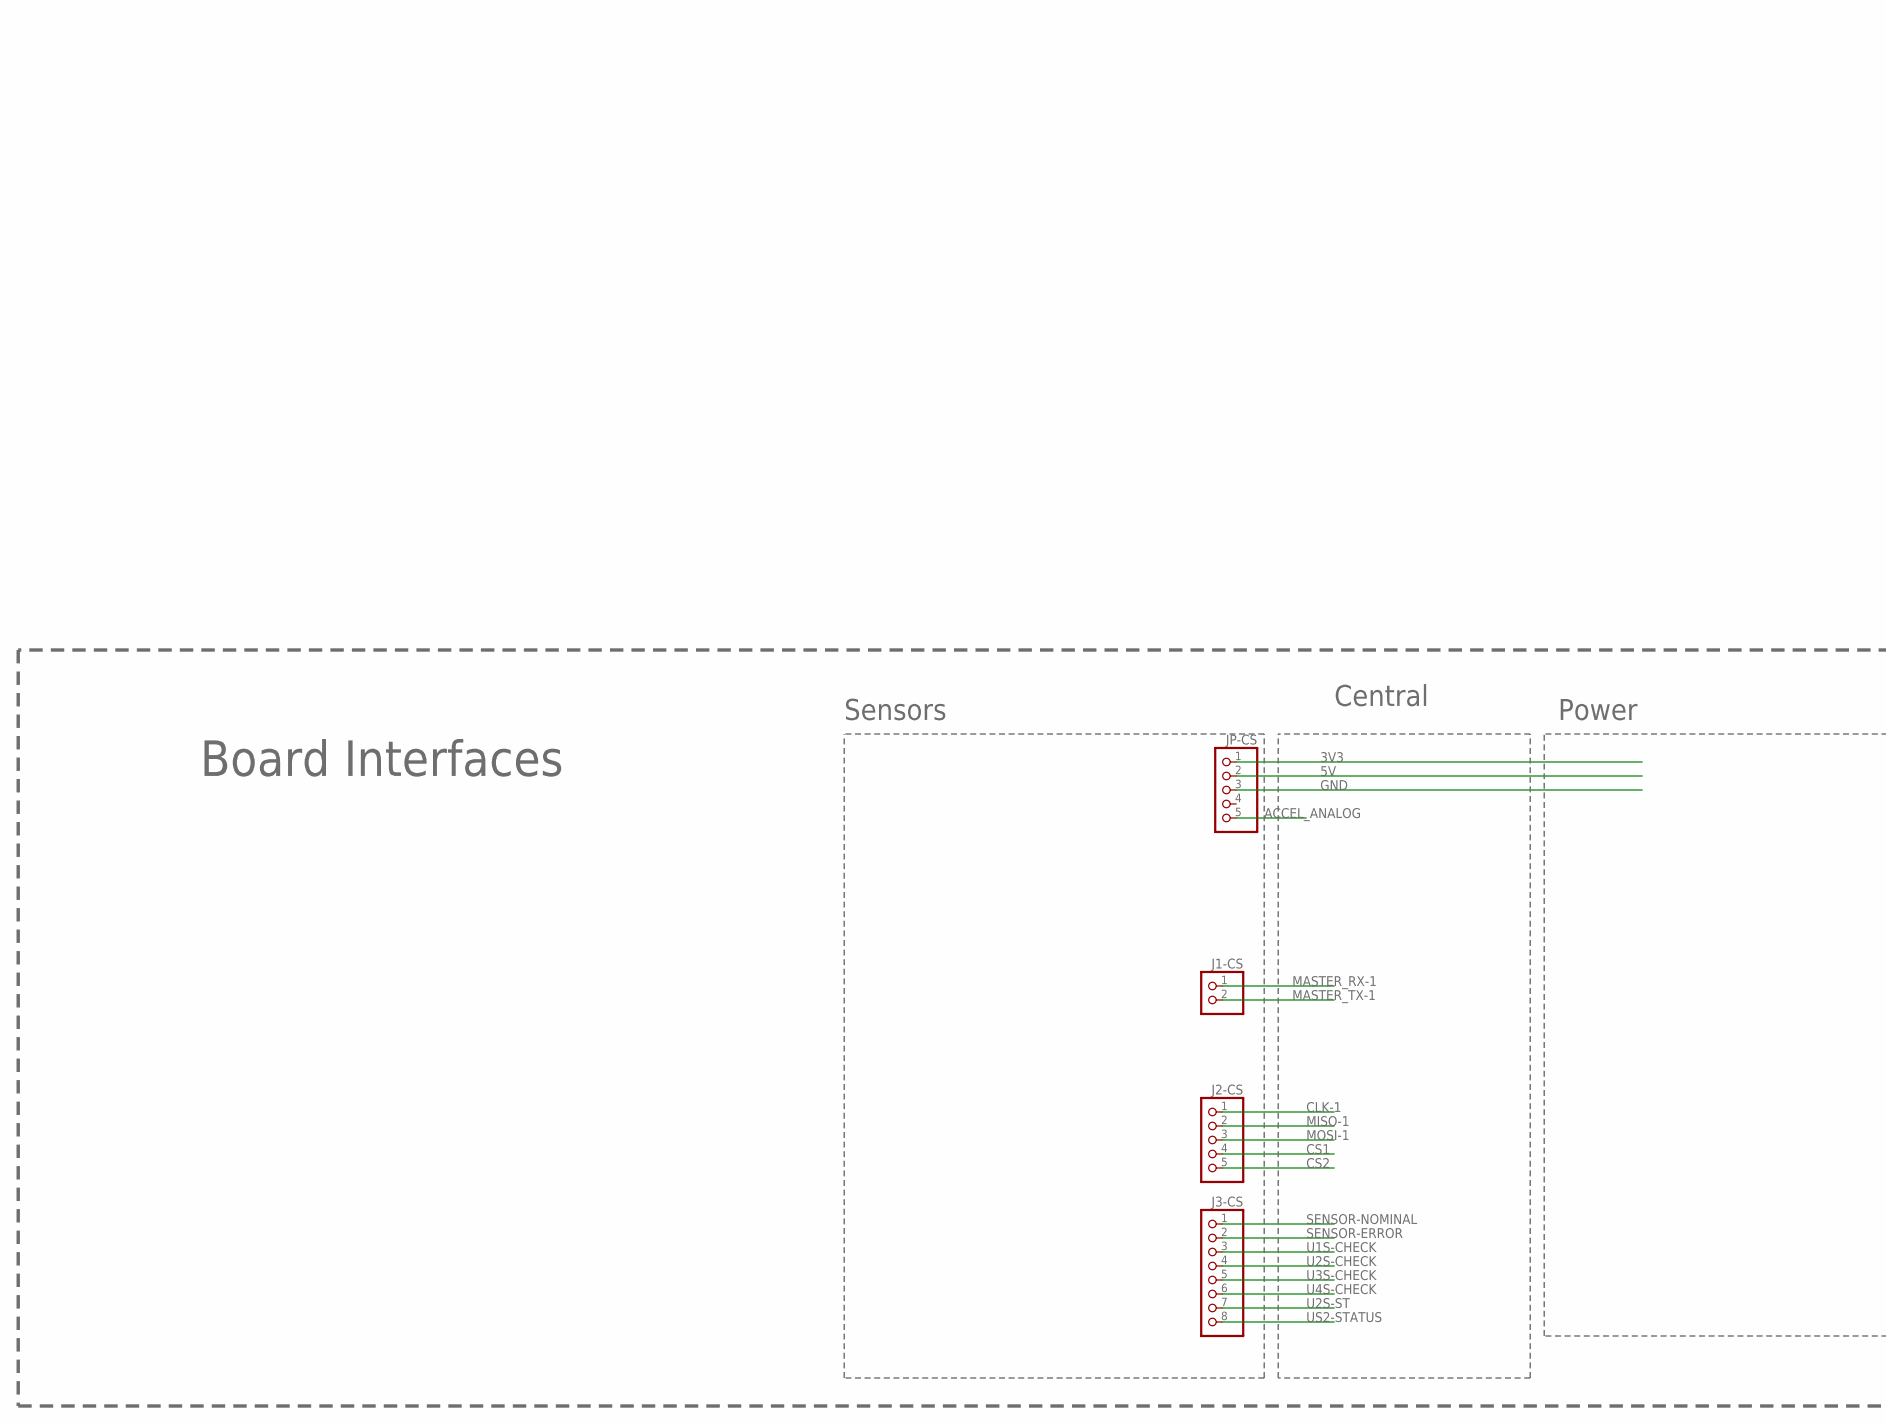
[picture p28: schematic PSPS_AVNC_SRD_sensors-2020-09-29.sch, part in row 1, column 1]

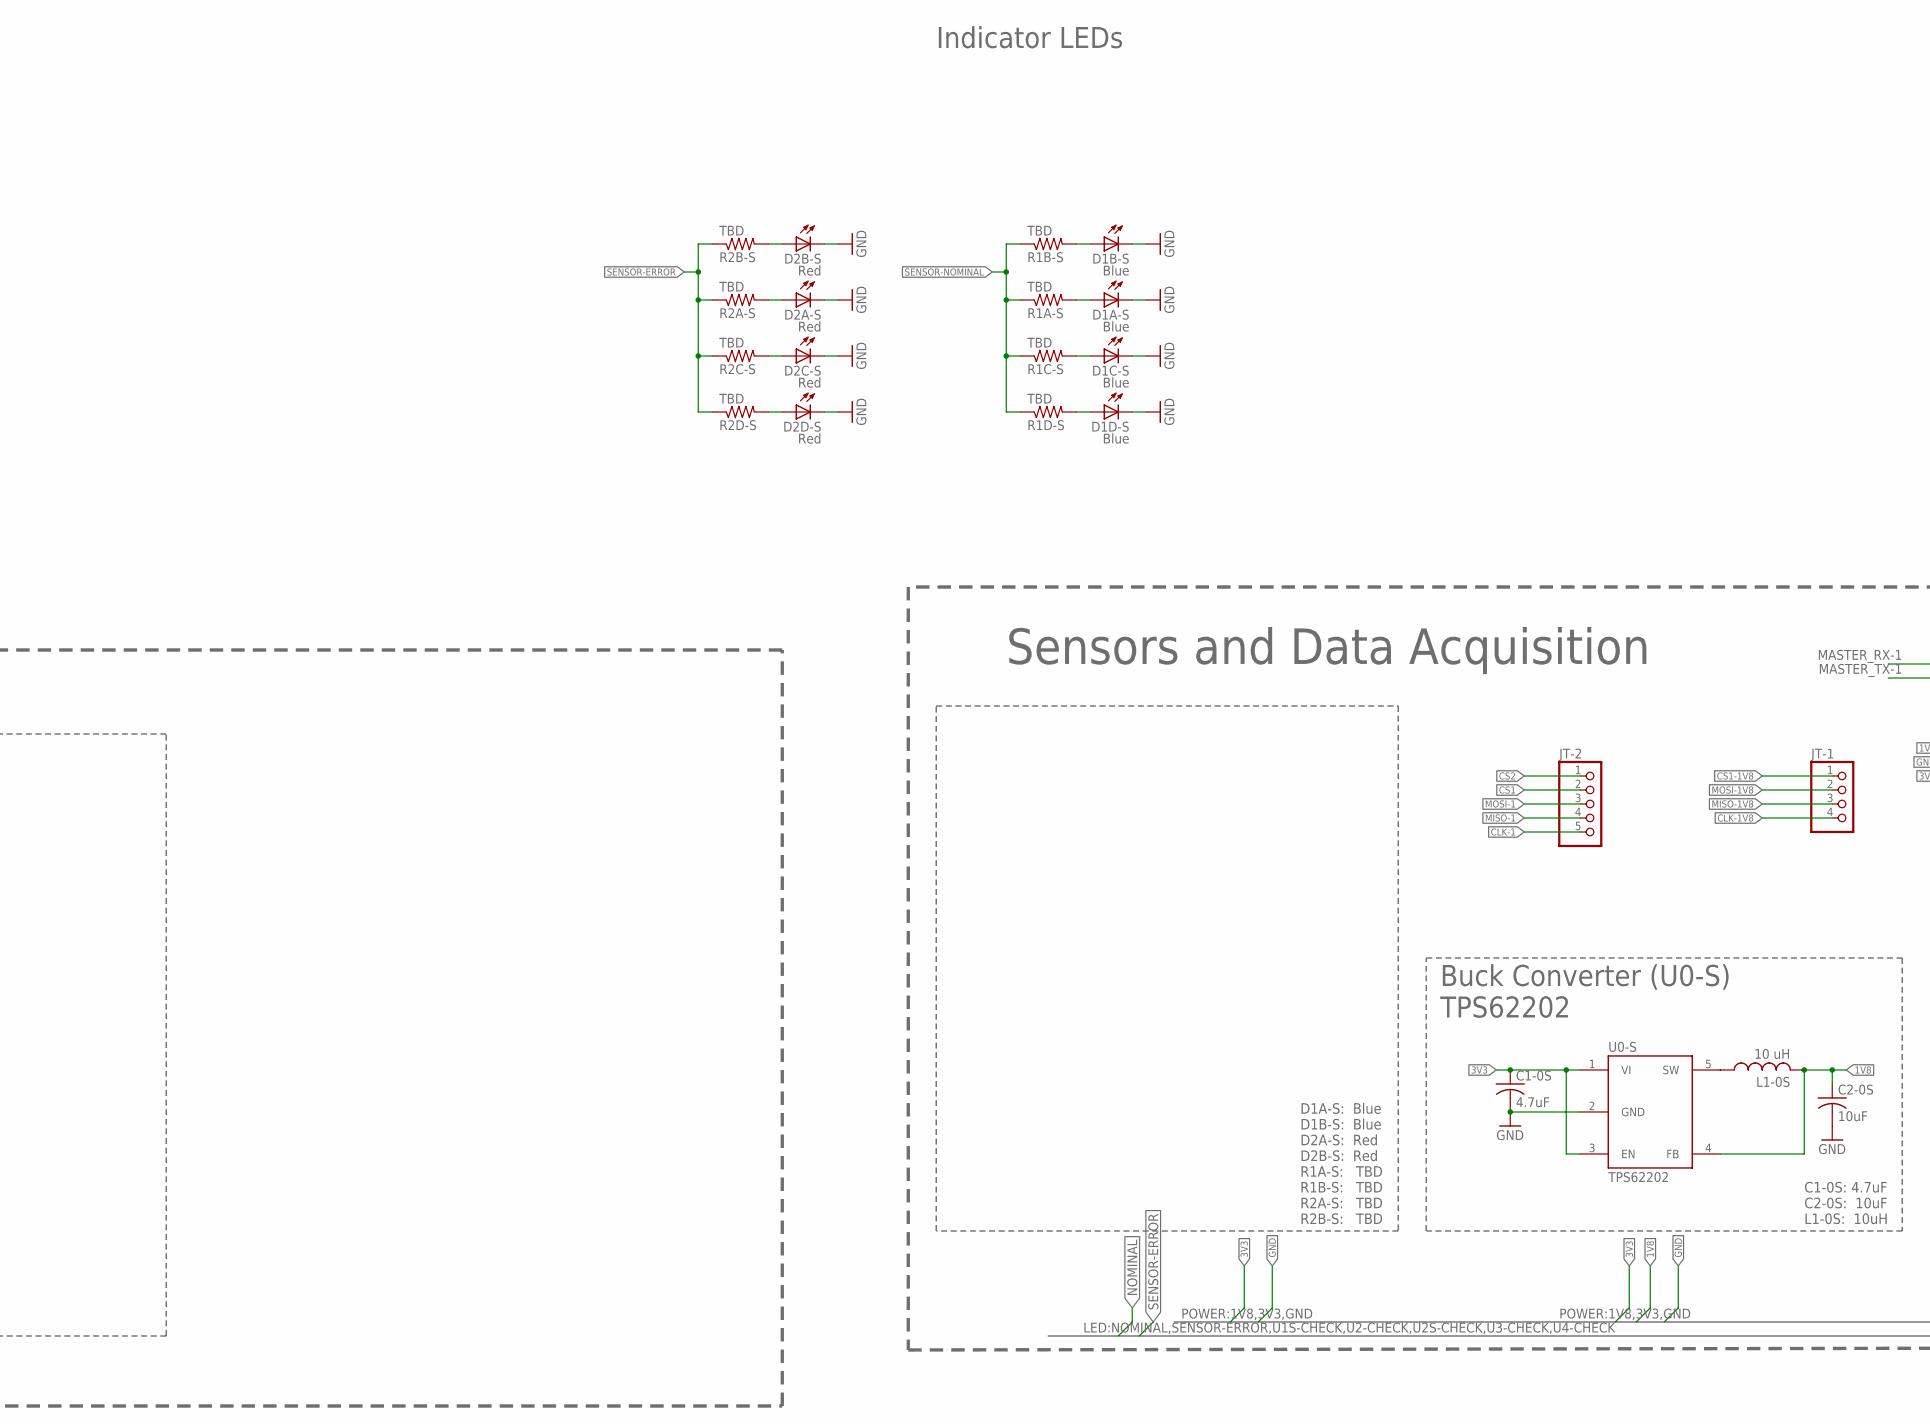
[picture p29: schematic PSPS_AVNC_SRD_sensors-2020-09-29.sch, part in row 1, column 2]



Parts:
AT1-S: A-1JB; A1JB
C1-0S: 4.7uF; C0805
C1-1S, C1-3S, C2-1S, C2-2S, C3-1S: 0.1uF; C0805
C1-2S: 0.01uF; C0805
C2-0S: 10uF; C0805
D1-1S, D1-2S, D1-3S, D1-4S: Green; CHIPLED_0805
D1A-S, D1B-S, D1C-S, D1D-S, D2A-1S, D2A-2S, D2A-3S, D2A-4S, D2B-1S, D2B-2S, D2B-3S, D2B-4S: Blue; CHIPLED_0805
D2A-S, D2B-S, D2C-S, D2D-S: Red; CHIPLED_0805
D3-4S: Yellow; CHIPLED_0805
J1-CS: PINHD-1X2; 1X02
J2-CS: PINHD-1X5; 1X05
J3-CS: PINHD-1X8; 1X08
JP-CS: PINHD-1X5; 1X05
JT-1: PINHD-1X4; 1X04
JT-2: PINHD-1X5; 1X05
JT-3: PINHD-1X2; 1X02
JT-P: PINHD-1X3; 1X03
L1-0S: 10 uH; L1812
Q1-1S: MMBTA06Q-7-F; SOT23
R1-1S, R1-2S, R1-3S, R1-4S, R1A-S, R1B-S, R1C-S, R1D-S, R2A-1S, R2A-2S, R2A-3S, R2A-4S, R2A-S, R2B-1S, R2B-2S, R2B-3S, R2B-4S, R2B-S, R2C-S, R2D-S, R3-1S, R3-4S: TBD; R0805
R3-2S: 1k; R0805
U0-S: TPS62202; SOT95P280X145-5
U1-S: ICM-20948; QFN40P300X300X105-25T159X175
U2-S: MMA1211KEG; SOIC127P1041X355-16N
U3-S: MS5607
U4-S: FGPMMOPA6H; SOIC127P1800X470-20N
U11-S, U12-S, U13-S, U14-S: SN74LV1T34; SOT65P210X110-5

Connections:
1V8: C2-0S.1, C2-1S.1, C3-1S.1, JT-P.1, L1-0S.2, R3-1S.2, U0-S.4 (FB), U1-S.8 (VDDIO), U1-S.13 (VDD), U11-S.5 (VCC), U12-S.5 (VCC), U14-S.5 (VCC)
3D-FIX: D3-4S.A, U4-S.5 (3D-FIX)
3V3: C1-0S.1, C1-3S.1, D1-3S.A, D1-4S.A, JP-CS.1, JT-P.3, R1-1S.1, U0-S.1 (VI), U0-S.3 (EN), U3-S.P$1 (VDD), U4-S.1 (VCC), U13-S.5 (VCC)
5V: C2-2S.1, D1-2S.A, JP-CS.2, U2-S.8 (VDD)
ACCEL_ANALOG: C1-2S.1, JP-CS.5, R3-2S.2
CLK-1: J2-CS.1, JT-2.5, U3-S.P$8 (SCLK), U14-S.2 (A)
CLK-1V8: JT-1.4, U1-S.23 (SCL/SCLK), U14-S.4 (Y)
CS1: J2-CS.4, JT-2.2, U11-S.2 (A)
CS1-1V8: JT-1.1, U1-S.22 (NCS), U11-S.4 (Y)
CS2: J2-CS.5, JT-2.1, U3-S.P$4 (CSB), U3-S.P$5 (CSB)
D1-2S_R1-2S: D1-2S.C, R1-2S.1
D1-3S_R1-3S: D1-3S.C, R1-3S.1
D1-4S_R1-4S: D1-4S.C, R1-4S.1
D2A-2S_R2A-2S: D2A-2S.C, R2A-2S.1
D2A-3S_R2A-3S: D2A-3S.C, R2A-3S.1
D2A-4S_R2A-4S: D2A-4S.C, R2A-4S.1
D3-4S_R3-4S: D3-4S.C, R3-4S.1
EX_ANT: AT1-S.1 (SIGNAL), U4-S.11 (EX_ANT)
GND: AT1-S.2 (GND_1), AT1-S.3 (GND_2), AT1-S.4 (GND_3), C1-0S.2, C1-1S.2, C1-2S.2, C1-3S.2, C2-0S.2, C2-1S.2, C2-2S.2, C3-1S.2, D1A-S.C, D1B-S.C, D1C-S.C, D1D-S.C, D2A-1S.C, D2A-S.C, D2B-1S.C, D2B-2S.C, D2B-3S.C, D2B-4S.C, D2B-S.C, D2C-S.C, D2D-S.C, JP-CS.3, JT-P.2, Q1-1S.3 (E), R1-2S.2, R1-3S.2, R1-4S.2, R2A-2S.2, R2A-3S.2, R2A-4S.2, R3-4S.2, U0-S.2 (GND), U1-S.18 (GND), U1-S.20 (RESV.GND), U2-S.7 (VSS), U3-S.P$2 (PS), U3-S.P$3 (GND), U4-S.3 (GND), U4-S.8 (GND), U4-S.12 (GND), U4-S.19 (GND), U11-S.3 (GND), U12-S.3 (GND), U13-S.3 (GND), U14-S.3 (GND)
MASTER_RX-1: J1-CS.1, JT-3.1, U4-S.9 (TX)
MASTER_TX-1: J1-CS.2, JT-3.2, U4-S.10 (RX)
MISO-1: J2-CS.2, JT-2.4, U3-S.P$6 (SDO), U13-S.4 (Y)
MISO-1V8: JT-1.3, U1-S.9 (SDO/AD0), U13-S.2 (A)
MOSI-1: J2-CS.3, JT-2.3, U3-S.P$7 (SDI), U12-S.2 (A)
MOSI-1V8: JT-1.2, U1-S.24 (SDA/SDI), U12-S.4 (Y)
R1-1S_Q1-1S: D1-1S.C, Q1-1S.2 (C)
R1A-S_D1A-S: D1A-S.A, R1A-S.2
R1B-S_D1B-S: D1B-S.A, R1B-S.2
R1C-S_D1C-S: D1C-S.A, R1C-S.2
R1D-S_D1D-S: D1D-S.A, R1D-S.2
R2-1S_D1-1S: D1-1S.A, R1-1S.2
R2A-1S_D2A-1S: D2A-1S.A, R2A-1S.2
R2A-S_D2A-S: D2A-S.A, R2A-S.2
R2B-1S_D2B-1S: D2B-1S.A, R2B-1S.2
R2B-2S_D2B-2S: D2B-2S.A, R2B-2S.2
R2B-3S_D2B-3S: D2B-3S.A, R2B-3S.2
R2B-4S_D2B-4S: D2B-4S.A, R2B-4S.2
R2B-S_D2B-S: D2B-S.A, R2B-S.2
R2C-S_D2C-S: D2C-S.A, R2C-S.2
R2D-S_D2D-S: D2D-S.A, R2D-S.2
R3-1S_Q1-1S: Q1-1S.1 (B), R3-1S.1
REGOUT: C1-1S.1, U1-S.10 (REGOUT)
SENSOR-ERROR: J3-CS.2, R2A-S.1, R2B-S.1, R2C-S.1, R2D-S.1
SENSOR-NOMINAL: J3-CS.1, R1A-S.1, R1B-S.1, R1C-S.1, R1D-S.1
U0S-SW: L1-0S.1, U0-S.5 (SW)
U1S-CHECK: J3-CS.3, R2A-1S.1, R2B-1S.1
U2S-CHECK: D2A-2S.A, J3-CS.4, R2B-2S.1
U2S-ST: J3-CS.7, U2-S.4 (ST)
U3S-CHECK: D2A-3S.A, J3-CS.5, R2B-3S.1
U4S-CHECK: D2A-4S.A, J3-CS.6, R2B-4S.1
US2-STATUS: J3-CS.8, U2-S.6 (STATUS)
VOUT: R3-2S.1, U2-S.5 (VOUT)

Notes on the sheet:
Level Shifters (U11-S, U12-S, U13-S, U14-S) SN74LV1T34
9 Axis IMU (U1-S) ICM-20948
Buck Converter (U0-S) TPS62202
C1-0S: 4.7uF C2-0S: 10uF L1-0S: 10uH
D1-1S: Green D2-1S: Blue R1-1S: TBD R2-1S: TBD C1-1S: 0.1uF C2-1S: 0.1uF C3-1S: 0.1uF
Linear Accelerometer (U2-S) MMA1211
D1-2S: Green D2-2S: Blue R1-2S: TBD R2-2S: TBD R3-2S: 1k C1-2S: 0.1uF C2-2S: 0.1uF
Digital Pressure Sensor (U3-S) MS5607
D1-3S: Green D2-3S: Blue R1-3S: TBD R2-3S: TBD C1-3S: 0.1uF
GPS Receiver (U4-S) FGPMMOPA6H Ext. Ant. Connector (AT1-S) A-1JB
D1-4S: Green D2-4S: Blue D3-4S: Yellow R1-4S: TBD R2-4S: TBD R3-4S: TBD
D1A-S: Blue D1B-S: Blue D2A-S: Red D2B-S: Red R1A-S: TBD R1B-S: TBD R2A-S: TBD R2B-S: TBD
Indicator LEDs
Sensors and Data Acquisition
Central
Power
Sensors
Board Interfaces



Board: 2 copper layers, 101.6 x 101.6 mm, 72 parts (51 on the bottom side), 52 nets.

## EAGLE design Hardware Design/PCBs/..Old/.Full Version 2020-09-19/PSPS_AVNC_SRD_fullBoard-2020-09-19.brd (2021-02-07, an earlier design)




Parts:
1S_LIPO: 1725656
AT1-S: A-1JB; A1JB
C1, C2: 4.3p; C0805
C1-0C, C2-0C, C3-0C, C4-0C, C5-0C, C6-0C, C7-0C, C8-0C, C9-0C, C10-0C, C11-0C, C12-0C, C15-0C: 100nF; C0805
C1-0S, C1-1P, C2-1P, C13-0C: 4.7uF; C0805
C1-1S, C1-2C, C1-3S, C2-1S, C2-2S, C3-1S: 0.1uF; C0805
C1-2P, C2-0S, C2-2P, C4-9P: 10uF; C0805
C1-2S: 0.01uF; C0805
C1-9P: 33pF; C0805
C1-11P: 47uF; C0805
C1-C: 100 nf; C0805
C2-9P: 6.8pF; C0805
C3-2P, C4-2P, C5-2P: 22pF; C0805
C3-9P: 4.7pF; C0805
C14-0C: 1 uF; C0805
C16-0C, C17-0C: 2.2uF; C0805
D0A-C, D0B-C, D0C-C, D2B-C, D5-C, D6-C: RED; CHIPLED_0805
D1-1P: TBD; CHIPLED_0805
D1-1S, D1-2S, D1-3S, D1-4S: Green; CHIPLED_0805
D1-11P: DFLS130L-7 (TBD); POWERDI_123
D1A-C, D1B-C, D2A-C: GREEN; CHIPLED_0805
D1A-S, D1B-S, D2-1S, D2-2S, D2-3S, D2-4S: Blue; CHIPLED_0805
D2A-S, D2B-S: Red; CHIPLED_0805
D3-4S: Yellow; CHIPLED_0805
D3-C: YELLOW; CHIPLED_0805
D4-C: BLUE; CHIPLED_0805
FB1-0C: MMZ2012Y152B; BEADC2012X105N
J1-9P: CONN_08X2; 2X8
J1-C: PINHD-1X6; 1X06
J1-CP, J2-CP, J3-CP: PINHD-1X4; 1X04
J1-CS: PINHD-1X2; 1X02
J2-C: 2134441-2; TE_2134441-2
J2-CS: PINHD-1X5; 1X05
J2-P: 1725711
J3-CS: PINHD-1X8; 1X08
JP-CP: PINHD-1X5; 1X05
JP-CS: PINHD-1X5; 1X05
L1-0S: 10 uH; PF0560NL
L1-2P: XFL4020-102MEB (1uH); XFL4020
L1-9P: LQM21PH2R2NGCD (2.2uH); INDC2012X100N
LS1-C: ASI09N27M-05Q
Q1-5P, Q1-6P: SI7232DN-T1-GE3; POWERPAK-1212-8
Q1-LS1C: MMBTA06Q-7-F; SOT23
R0-0C, R1-0C, R1-2C, R2-2C, R3-2C, R4-2C: 10K; R0805
R0A-C, R0B-C, R0C-C, R1A-C, R1B-C, R2A-C, R2B-C, R3-C, R4-C, R5-C, R6-C: TBD; M0805
R1-1P: 1K; R0805
R1-1S, R1-2S, R1-3S, R1-4S, R1A-S, R1B-S, R2-1S, R2-2S, R2-3S, R2-4S, R2A-S, R2B-S, R3-4S: TBD; R0805
R1-2P: 187k; R0805
R1-5P, R1-6P, R5-5P, R5-6P: 3.3K; M0805
R1-9P: 562k; R0805
R1-11P, R1-LS1C, R3-9P, R3-LS1C: 10k; R0805
R1-J1C, R1-J2C, R2-J1C, R2-J2C, R3-J1C, R4-J1C: 22; M0805
R2-1P: 2K; R0805
R2-2P: 35.6k; R0805
R2-5P, R2-6P, R6-5P, R6-6P: 1K; M0805
R2-9P, R3-11P, R4-11P: 100k; R0805
R2-11P: 8.06k; R0805
R2-LS1C, R3-2S: 1k; R0805
R3-5P, R3-6P, R7-5P, R7-6P: 100K; M0805
R3-J2C: 1.5K; M0805
R4-5P, R4-6P, R8-5P, R8-6P: 27K; M0805
R4-9P: 9.09k; R0805
S0-0C: DISARM; B3F-10XX
S1-0C: 10-XX; B3F-10XX
S1-P: EG1218S; EG1218
U0-C: STM32F429ZIT6; QFP50P2200X2200X160-144N
U0-S: TPS62202; SOT95P280X145-5
U1-C: TC58CVG2S0HRAIJ; SON127P800X600X80-9N
U1-P: MCP73831; SOT95P270X145-5N
U1-S: ICM-20948; QFN40P300X300X105-25T159X175
U2-C: ADS1015BQDGSRQ1; SOP50P490X110-10N
U2-P: ISL91110IRAZ-T7A; QFN50P400X400X100-21N
U2-S: MMA1211KEG; SOIC127P1041X355-16N
U3-S: MS5607
U4-S: FGPMMOPA6H; SOIC127P1800X470-20N
U7-P, U8-P: LM293DR; SOIC127P600X175-8N
U9-P: LM3671-ADJ; SOT95P280X145-5N
U11-S, U12-S, U13-S, U14-S: SN74LV1T34; SOT65P210X110-5
VR1-LS1C: TRIM_US-LI10; LI10
Y1-C: NX3225GD-8MHZ-STD-CRA-3; 3.2X2.5_KX-7

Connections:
1V8: C2-0S.1, C2-1S.1, C3-1S.1, D1-1S.A, L1-0S.P$2 (2), U0-S.4 (FB), U1-S.8 (VDDIO), U1-S.13 (VDD), U12-S.5 (VCC), U13-S.5 (VCC), U14-S.5 (VCC)
3D-FIX: D3-4S.A, U4-S.5 (3D-FIX)
3V3: C1-0C.1, C1-0S.1, C1-2C.1, C1-3S.1, C1-9P.1, C1-C.1, C2-0C.1, C3-0C.1, C4-0C.1, C4-9P.1, C5-0C.1, C6-0C.1, C7-0C.1, C8-0C.1, C9-0C.1, C10-0C.1, C11-0C.1, C12-0C.1, C13-0C.1, C14-0C.1, D1-2S.A, D1-3S.A, D1-4S.A, FB1-0C.1, J1-C.4, JP-CP.1, JP-CS.1, L1-9P.2, R1-2C.1, R1-9P.2, R2-2C.1, R3-9P.2, R3-J2C.2, R4-2C.1, S0-0C.1 (S), U0-C.6 (VBAT), U0-C.17 (VDD_1), U0-C.30 (VDD_2), U0-C.39 (VDD_3), U0-C.52 (VDD_4), U0-C.62 (VDD_5), U0-C.72 (VDD_6), U0-C.84 (VDD_7), U0-C.95 (VDD_8), U0-C.108 (VDD_9), U0-C.121 (VDD_10), U0-C.131 (VDD_11), U0-C.143 (PDR_ON), U0-C.144 (VDD_12), U0-S.1 (VI), U0-S.3 (EN), U1-C.7 (VCC), U2-C.8 (VDD), U3-S.P$1 (VDD), U4-S.1 (VCC), U7-P.8 (VCC), U8-P.8 (VCC), U11-S.5 (VCC)
5V: C2-2S.1, C3-2P.1, C3-9P.1, C4-2P.1, C5-2P.1, J1-9P.14, JP-CP.2, JP-CS.2, R1-2P.2, U2-P.17 (VOUT_1), U2-P.18 (VOUT_2), U2-P.19 (VOUT_3), U2-P.20 (VOUT_4), U2-S.8 (VDD), U9-P.1 (VIN), U9-P.3 (EN), VR1-LS1C.A
ACCEL_ANALOG: C1-2S.1, JP-CS.5, R3-2S.2, U0-C.46 (PB0)
ADC-ERROR: D6-C.A, U0-C.59 (PE8)
ADC_ALERT: R4-2C.2, U0-C.98 (PC8), U2-C.2 (ALERT/RDY)
ADDR: R3-2C.2, U2-C.1 (ADDR)
ARMED-LED: D0A-C.A, D0B-C.A, D0C-C.A, U0-C.53 (PF13)
BATT_MEAS: JP-CP.5, R3-11P.1, R4-11P.2, U0-C.47 (PB1)
BOOT0: R1-0C.1, U0-C.138 (BOOT0)
BUZZER_OUT: R1-LS1C.1, U0-C.1 (PE2)
CENTRAL-ERROR: D2A-C.A, D2B-C.A, U0-C.55 (PF15)
CENTRAL-NOMINAL: D1A-C.A, D1B-C.A, U0-C.54 (PF14)
CLK-1: J2-CS.1, U0-C.41 (PA5), U3-S.P$8 (SCLK), U13-S.2 (A)
CLK-1V8: U1-S.23 (SCL/SCLK), U13-S.4 (Y)
CLK-3: U0-C.111 (PC10), U1-C.6 (SCK)
CMP_LDO_IN: R1-11P.1, R2-11P.2, U7-P.3 (1IN+), U7-P.5 (2IN+), U8-P.3 (1IN+), U8-P.5 (2IN+)
CMP_LDO_OUT_1: Q1-5P.2 (G1), R2-5P.2, U7-P.1 (1OUT)
CMP_LDO_OUT_2: Q1-5P.4 (G2), R6-5P.2, U7-P.7 (2OUT)
CMP_LDO_OUT_3: Q1-6P.2 (G1), R2-6P.2, U8-P.1 (1OUT)
CMP_LDO_OUT_4: Q1-6P.4 (G2), R6-6P.2, U8-P.7 (2OUT)
CMP_RAIL: R3-9P.1, R4-9P.2, U7-P.2 (1IN-), U7-P.6 (2IN-), U8-P.2 (1IN-), U8-P.6 (2IN-)
CS1: J2-CS.4, U0-C.44 (PC4), U14-S.2 (A)
CS1-1V8: U1-S.22 (NCS), U14-S.4 (Y)
CS2: J2-CS.5, U0-C.45 (PC5), U3-S.P$4 (CSB), U3-S.P$5 (CSB)
CS-3: U0-C.114 (PD0), U1-C.1 (!CS)
CTS: J1-9P.13, J1-CP.4, U0-C.34 (PA0)
D0A-C_R0A-C: D0A-C.C, R0A-C.1
D0B-C_R0B-C: D0B-C.C, R0B-C.1
D0C-C_R0C-C: D0C-C.C, R0C-C.1
D1-1P_R1-1P: D1-1P.C, R1-1P.1
D1-1S_R1-1S: D1-1S.C, R1-1S.1
D1-2S_R1-2S: D1-2S.C, R1-2S.1
D1-3S_R1-3S: D1-3S.C, R1-3S.1
D1-4S_R1-4S: D1-4S.C, R1-4S.1
D1A-C_R1A-C: D1A-C.C, R1A-C.1
D1A-S_R1A-S: D1A-S.C, R1A-S.1
D1B-C_R1B-C: D1B-C.C, R1B-C.1
D1B-S_R1B-S: D1B-S.C, R1B-S.1
D2-1S_R2-1S: D2-1S.C, R2-1S.1
D2-2S_R2-2S: D2-2S.C, R2-2S.1
D2-3S_R2-3S: D2-3S.C, R2-3S.1
D2-4S_R2-4S: D2-4S.C, R2-4S.1
D2A-C_R2A-C: D2A-C.C, R2A-C.1
D2A-S_R2A-S: D2A-S.C, R2A-S.1
D2B-C_R2B-C: D2B-C.C, R2B-C.1
D2B-S_R2B-S: D2B-S.C, R2B-S.1
D3-4S_R3-4S: D3-4S.C, R3-4S.1
D3-C_R3-C: D3-C.C, R3-C.1
D4-C_R4-C: D4-C.C, R4-C.1
D5-C_R5-C: D5-C.C, R5-C.1
D6-C_R6-C: D6-C.C, R6-C.1
D+: R2-J2C.2, R3-J2C.1, U0-C.104 (PA12)
D+_R2-J1C: J2-C.3 (D+), R2-J2C.1
D-: R1-J2C.2, U0-C.103 (PA11)
D-_R1-J1C: J2-C.2 (D-), R1-J2C.1
DISARM_INPUT: R0-0C.2, S0-0C.3, U0-C.89 (PG4)
DROGUE-LED: D3-C.A, U0-C.56 (PG0)
EX_ANT: AT1-S.1 (SIGNAL), U4-S.11 (EX_ANT)
FET_A: J2-P.2, Q1-5P.7 (D1_1), Q1-5P.8 (D1_2), R3-5P.1
FET_B: J2-P.4, Q1-5P.5 (D2_1), Q1-5P.6 (D2_2), R7-5P.1
FET_C: J2-P.6, Q1-6P.7 (D1_1), Q1-6P.8 (D1_2), R3-6P.1
FET_D: J2-P.8, Q1-6P.5 (D2_1), Q1-6P.6 (D2_2), R7-6P.1
FIRE_A: J2-CP.1, R1-5P.2, R2-5P.1, U0-C.11 (PF1)
FIRE_B: J2-CP.2, R5-5P.2, R6-5P.1, U0-C.12 (PF2)
FIRE_C: J2-CP.3, R1-6P.2, R2-6P.1, U0-C.13 (PF3)
FIRE_D: J2-CP.4, R5-6P.2, R6-6P.1, U0-C.14 (PF4)
GND: 1S_LIPO.2, AT1-S.2 (GND_1), AT1-S.3 (GND_2), AT1-S.4 (GND_3), C1.2, C1-0C.2, C1-0S.2, C1-1P.2, C1-1S.2, C1-2C.2, C1-2P.2, C1-2S.2, C1-3S.2, C1-11P.2, C1-C.2, C2.2, C2-0C.2, C2-0S.2, C2-1P.2, C2-1S.2, C2-2P.2, C2-2S.2, C2-9P.2, C3-0C.2, C3-1S.2, C3-9P.2, C4-0C.2, C4-2P.2, C4-9P.2, C5-0C.2, C5-2P.2, C6-0C.2, C7-0C.2, C8-0C.2, C9-0C.2, C10-0C.2, C11-0C.2, C12-0C.2, C13-0C.2, C14-0C.2, C15-0C.2, C16-0C.2, C17-0C.2, J1-9P.15, J1-C.1, J2-C.5 (GND), J2-C.S1 (SHIELD), J2-C.S2 (SHIELD), J2-C.S3 (SHIELD), J2-C.S4 (SHIELD), JP-CP.3, JP-CS.3, LS1-C.V-, Q1-5P.1 (S1), Q1-5P.3 (S2), Q1-6P.1 (S1), Q1-6P.3 (S2), R0-0C.1, R0A-C.2, R0B-C.2, R0C-C.2, R1-0C.2, R1-1S.2, R1-2S.2, R1-3S.2, R1-4S.2, R1-5P.1, R1-6P.1, R1A-C.2, R1A-S.2, R1B-C.2, R1B-S.2, R2-1P.1, R2-1S.2, R2-2P.1, R2-2S.2, R2-3S.2, R2-4S.2, R2-9P.1, R2-11P.1, R2A-C.2, R2A-S.2, R2B-C.2, R2B-S.2, R3-2C.1, R3-4S.2, R3-11P.2, R3-C.2, R3-LS1C.1, R4-5P.1, R4-6P.1, R4-9P.1, R4-C.2, R5-5P.1, R5-6P.1, R5-C.2, R6-C.2, R8-5P.1, R8-6P.1, S1-0C.3, S1-0C.4 (P1), U0-C.16 (VSS_1), U0-C.31 (VSSA), U0-C.38 (VSS_2), U0-C.51 (VSS_3), U0-C.61 (VSS_4), U0-C.83 (VSS_5), U0-C.94 (VSS_6), U0-C.107 (VSS_7), U0-C.120 (VSS_8), U0-C.130 (VSS_9), U0-S.2 (GND), U1-C.8 (VSS), U1-P.2 (VSS), U1-S.18 (GND), U1-S.20 (RESV.GND), U2-C.3 (GND), U2-P.3 (PGND), U2-P.12 (MODE), U2-P.13 (SGND_1), U2-S.7 (VSS), U3-S.P$2 (PS), U3-S.P$3 (GND), U4-S.3 (GND), U4-S.8 (GND), U4-S.12 (GND), U4-S.19 (GND), U7-P.4 (GND), U8-P.4 (GND), U9-P.2 (GND), U11-S.3 (GND), U12-S.3 (GND), U13-S.3 (GND), U14-S.3 (GND)
HOLD: U0-C.77 (PD8), U1-C.5 (!HOLD!/IO3)
ID: J2-C.4 (ID), U0-C.102 (PA10)
J1-C_R1-J1C: J1-C.5, R1-J1C.1
J1-C_R2-J1C: J1-C.6, R2-J1C.1
MAIN-LED: D4-C.A, U0-C.57 (PG1)
MASTER_RX-1: J1-CS.1, U0-C.97 (PC7), U4-S.9 (TX)
MASTER_RX-2: J1-9P.7, J1-CP.2, U0-C.37 (PA3)
MASTER_TX-1: J1-CS.2, U0-C.96 (PC6), U4-S.10 (RX)
MASTER_TX-2: J1-9P.9, J1-CP.3, U0-C.36 (PA2)
MISO-1: J2-CS.2, U0-C.42 (PA6), U11-S.4 (Y)
MISO-1V8: U1-S.9 (SDO/AD0), U11-S.2 (A)
MISO-3: U0-C.112 (PC11), U1-C.2 (SO/IO1)
MOSI-1: J2-CS.3, U0-C.43 (PA7), U3-S.P$6 (SDO), U3-S.P$7 (SDI), U12-S.2 (A)
MOSI-1V8: U1-S.24 (SDA/SDI), U12-S.4 (Y)
MOSI-3: U0-C.113 (PC12), U1-C.4 (SI/IO0)
NRST: C15-0C.1, R2-J1C.2, S1-0C.1 (S), S1-0C.2 (S1), U0-C.25 (NRST)
OSC_IN: C1.1, U0-C.23 (PH0), Y1-C.3 (2)
OSC_OUT: C2.1, U0-C.24 (PH1), Y1-C.1
Q1-LS1C_R2-LS1C: Q1-LS1C.3 (E), R2-LS1C.2
R1-LS1C_Q1-LS1C: Q1-LS1C.1 (B), R1-LS1C.2
R2-LS1C_LS1-C: LS1-C.V+, R2-LS1C.1
REGOUT: C1-1S.1, U1-S.10 (REGOUT)
RTS: J1-9P.5, J1-CP.1, U0-C.35 (PA1)
SCL-1: R2-2C.2, U0-C.100 (PA8), U2-C.10 (SCL)
SDA-1: R1-2C.2, U0-C.99 (PC9), U2-C.9 (SDA)
SENSE_A: J3-CP.1, R3-5P.2, R4-5P.2, U0-C.18 (PF6), U2-C.4 (AIN0)
SENSE_B: J3-CP.2, R7-5P.2, R8-5P.2, U0-C.19 (PF7), U2-C.5 (AIN1)
SENSE_C: J3-CP.3, R3-6P.2, R4-6P.2, U0-C.20 (PF8), U2-C.6 (AIN2)
SENSE_D: J3-CP.4, R7-6P.2, R8-6P.2, U0-C.21 (PF9), U2-C.7 (AIN3)
SENSOR-ERROR: D2A-S.A, D2B-S.A, U0-C.64 (PE11)
SENSOR-NOMINAL: D1A-S.A, D1B-S.A, U0-C.63 (PE10)
SENSOR_ERROR: J3-CS.2
SENSOR_NOMINAL: J3-CS.1
STORAGE-ERROR: D5-C.A, U0-C.58 (PE7)
SWCLK: J1-C.2, R4-J1C.1, R4-J1C.2, U0-C.109 (PA14)
SWDIO: J1-C.3, R3-J1C.1, R3-J1C.2, U0-C.105 (PA13)
SWO: R1-J1C.2, U0-C.133 (PB3)
U0S-SW: L1-0S.P$1 (1), U0-S.5 (SW)
U1P-PROG: R2-1P.2, U1-P.5 (PROG)
U1P-STAT: R1-1P.2, U1-P.1 (STAT)
U1S-CHECK: D2-1S.A, J3-CS.3, U0-C.65 (PE12)
U2P-FB: C3-2P.2, R1-2P.1, R2-2P.2, U2-P.15 (FB)
U2S-CHECK: D2-2S.A, J3-CS.4, U0-C.66 (PE13)
U2S-ST: J3-CS.7, U0-C.69 (PB10), U2-S.4 (ST)
U3S-CHECK: D2-3S.A, J3-CS.5, U0-C.67 (PE14)
U4S-CHECK: D2-4S.A, J3-CS.6, U0-C.68 (PE15)
U9P-FB: C1-9P.2, C2-9P.1, R1-9P.1, R2-9P.2, U9-P.4 (FB)
U9P-LX1_1: L1-2P.2, U2-P.4 (LX1_1)
U9P-LX2_1: L1-2P.1, U2-P.1 (LX2_1)
U9P-SW: L1-9P.1, U9-P.5 (SW)
US2-STATUS: J3-CS.8, U0-C.70 (PB11), U2-S.6 (STATUS)
VBAT: 1S_LIPO.1, C2-1P.1, J2-P.1, J2-P.3, J2-P.5, J2-P.7, S1-P.P, U1-P.3 (VBAT)
VBAT_AFTER_SWITCH: D1-11P.2 (A), R4-11P.1, S1-P.S
VCAP_1: C16-0C.1, U0-C.71 (VCAP_1)
VCAP_2: C17-0C.1, U0-C.106 (VCAP_2)
VDDA: FB1-0C.2, U0-C.32 (VREF+), U0-C.33 (VDDA)
VOUT: R3-2S.1, U2-S.5 (VOUT)
VR1-LS1C: Q1-LS1C.2 (C), VR1-LS1C.S
VR1-LS1C_R3-LS1C: R3-LS1C.2, VR1-LS1C.E
VUSB: C1-1P.1, D1-1P.A, J2-C.1 (VBUS), JP-CP.4, U1-P.4 (VDD)
V_LDO_IN: C1-2P.1, C1-11P.1, C2-2P.1, D1-11P.1 (K), R1-11P.2, U2-P.6 (PVIN_1), U2-P.7 (PVIN_2), U2-P.8 (PVIN_3), U2-P.9 (PVIN_4), U2-P.10 (VIN), U2-P.11 (EN)
WP: U0-C.78 (PD9), U1-C.3 (!WP!/IO2)

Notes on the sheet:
Level Shifters (U11-S, U12-S, U13-S, U14-S) SN74LV1T34
9 Axis IMU (U1-S) ICM-20948
Buck Converter (U0-S) TPS62202
C1-0S: 4.7uF C2-0S: 10uF L1-0S: 10uH
D1-1S: Green D2-1S: Blue R1-1S: TBD R2-1S: TBD C1-1S: 0.1uF C2-1S: 0.1uF C3-1S: 0.1uF
Linear Accelerometer (U2-S) MMA1211
D1-2S: Green D2-2S: Blue R1-2S: TBD R2-2S: TBD R3-2S: 1k C1-2S: 0.1uF C2-2S: 0.1uF
Digital Pressure Sensor (U3-S) MS5607
D1-3S: Green D2-3S: Blue R1-3S: TBD R2-3S: TBD C1-3S: 0.1uF
GPS Receiver (U4-S) FGPMMOPA6H Ext. Ant. Connector (AT1-S) A-1JB
D1-4S: Green D2-4S: Blue D3-4S: Yellow R1-4S: TBD R2-4S: TBD R3-4S: TBD
D1A-S: Blue D1B-S: Blue D2A-S: Red D2B-S: Red R1A-S: TBD R1B-S: TBD R2A-S: TBD R2B-S: TBD
Indicator LEDs
Sensors and Data Acquisition
Central Processing
Power Systems and Deployment
placed in between each Vdd and Vss
Deployment (Q5-P)
R1-5P: 3.3K R2-5P: 1K R3-5P: 100K R4-5P: 27K R5-5P: 3.3K R6-5P: 1K R7-5P: 100K R8-5P: 27K Q1-5P: TBD
Processor
Storage
Decoupling Capacitors
SWD Programming
LEDs
ADC
USB Connector
1725711 - 8 Pin Terminal Block (3P)
MCP73831 - Charge Managment (U1-P)
D1-1P: TBD R1-1P: 1K R2-1P: 2K C1-1P: 4.7uF C2-1P: 4.7uF
LM3671-ADJ - Step Down (U9-P)
R1-9P: 562k R2-9P: 100k R3-9P: 10k R4-9P: 9.09k C1-9P: 33pF C2-9P: 6.8pF C3-9P: 4.7pF C4-9P: 10uF L1-9P: 2.2uH
LM293DR - Comparator (U7-P)
ISL91110IRAZ-T7A - Boost Converter (U2-P)
R1-10P: 187k R2-10P: 35.6k C1-10P: 10uF C2-10P: 10uF C3-10P: 22pF C4-10P: 22pF C5-10P: 22pF L1-10P: 1uH
VBAT to V_LDO_IN and CMP_LDO_IN (11P)
D1-11P: TBD R1-11P: 10k R2-11P: 8.0k R3-11P: 100k R4-11P: 100k C1-11P: 47uF
Deployment (Q6-P)
R1-6P: 3.3K R2-6P: 1K R3-6P: 100K R4-6P: 27K R5-6P: 3.3K R6-6P: 1K R7-6P: 100K R8-6P: 27K Q1-6P: TBD
LM293DR - Comparator (U8-P)
1725711 - 8 Pin Terminal Block (Radio) (9P)

Board: 2 copper layers, 180 parts (4 on the bottom side), 129 nets, no tracks yet.

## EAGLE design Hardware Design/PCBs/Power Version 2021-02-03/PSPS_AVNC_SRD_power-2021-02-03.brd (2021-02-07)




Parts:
1S_LIPO, 1S_LIPO1: 1725656
C1-1P, C2-1P: 4.7uF; C0805
C1-9P: 33pF; C0805
C1-11P, C4-9P3: 47uF; C0805
C2-9P: 6.8pF; C0805
C3-9P: 4.7pF; C0805
C4-9P: 10uF; C0805
C4-9P1: 100uF; C0805
C4-9P2: 10nF; C0805
CIN: uF; C0805
COUT: uF; C0805
D0, D1, D2, D3, D4, D5, D6, D7, D8, D9, D10, D11, D12, D13, D14, D15: LEDCHIPLED_0805; CHIPLED_0805
D1-1P, D1-1P1, D1-1P2, D1-1P5: GREEN; CHIPLED_0805
D1-1P3, D1-1P4: YELLOW; CHIPLED_0805
D1-1P6, D1-1P7, D1-1P8, D1-1P9, D1-1P10, D1-1P11: RED; CHIPLED_0805
D1-11P: DFLS130L-7 (TBD); POWERDI_123
IC1: NE555SOIC8; SOIC127P599X175-8
J1-9P: CONN_08X2; 2X8
J1-CP, J2-CP, J3-CP: PINHD-1X4; 1X04
J2-P: 1725711
JP-CP: PINHD-1X5; 1X05
L1-9P: LQM21PH2R2NGCD (2.2uH); INDC2012X100N
P-CHANNEL_MOSFET1: PMN40XPEA
Q1-5P, Q1-6P: SI7232DN-T1-GE3; POWERPAK-1212-8
R1, R1-11P, R1-11P1, R1-11P4, R1-11P8, R1-11P9, R1-11P13, R3-9P, R4, R5, R7, R9, R13: 10k; R0805
R1-1P: 12k; R0805
R1-5P, R1-6P, R5-5P, R5-6P: 3.3K; M0805
R1-9P: 562k; R0805
R1-11P2, R1-11P3, R1-11P6, R1-11P10, R1-11P11, R1-11P12, R1-11P14, R1-11P15, R1-11P16, R1-11P17: TBD; R0805
R1-11P5, R1-11P7, R2-9P, R3-11P, R3-11P1, R3-11P2, R3-11P3, R3-11P4, R4-11P, R11, R12: 100k; R0805
R2: 22k; R0805
R2-1P: 2K; R0805
R2-5P, R2-6P, R6-5P, R6-6P: 1K; M0805
R2-11P: 8.06k; R0805
R3: 82k; R0805
R4-5P, R4-6P, R8-5P, R8-6P: 100K; M0805
R4-9P: 9.09k; R0805
R5-11P: 0k; R0805
R6: 1k; R0805
R8, R10: 2.2k; R0805
R-EXT: 100k; R0805
S1-P: EG1218S; EG1218
SW1, SW2: SW_DIP-5; EDG-05
SW3: SW_DIP-2; EDG-02
TERMINALBLOCK: 1725656
U1-P: MCP73831; SOT95P270X145-5N
U7-P, U7-P1, U8-P, U8-P1, U8-P2: LM293DR; SOIC127P600X175-8N
U9-P: LM3671-ADJ; SOT95P280X145-5N
U$1: AP1501-33K5G-13; TO185P1524X485-6N
U$2: AP1501-50K5G-13; TO185P1524X485-6N
U$3, U$4, U$5, U$6, U$7, U$10, U$11, U$13, U$14, U$15, U$16, U$17, U$18: NPN_TRANSISTOR; SOT23
U$8, U$9, U$12: PNP_TRANSISTOR; SOT23
U$19, U$21: CD4050B; SOIC127P600X175-16N
U$20: TLC5926TSSOP; SOP65P640X120-24N

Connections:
3V3: C1-9P.1, C4-9P.1, C4-9P1.1, COUT.1, D0.A, D1.A, D14.A, D15.A, IC1.8 (VCC+), JP-CP.1, L1-9P.2, R1-9P.2, R1-11P6.2, R1-11P10.2, R1-11P11.2, R1-11P13.2, R1-11P14.2, R1-11P15.2, R1-11P16.2, R1-11P17.2, R2.2, R3-9P.2, R3-11P1.2, R3-11P2.2, R3-11P3.2, R3-11P4.2, R7.2, R10.1, R11.2, R12.2, SW1.1, SW1.2, SW1.3, SW1.4, SW1.5, SW2.1, SW2.2, SW2.3, SW2.4, SW2.5, SW3.1, SW3.2, TERMINALBLOCK.2, U7-P.8 (VCC), U7-P1.8 (VCC), U8-P.8 (VCC), U8-P1.2 (1IN-), U8-P1.6 (2IN-), U8-P1.8 (VCC), U8-P2.2 (1IN-), U8-P2.6 (2IN-), U8-P2.8 (VCC), U$1.4 (FB), U$8.2 (E), U$9.2 (E), U$12.2 (E), U$19.1 (VCC), U$20.24 (VDD), U$21.1 (VCC)
5V: C3-9P.1, J1-9P.14, JP-CP.2, U9-P.1 (VIN), U9-P.3 (EN)
ARMING_CHARGE: C4-9P1.2, R1-11P1.2, R3.2, U7-P1.6 (2IN-), U$9.3 (C)
ARM_GPIO: R4.2, R5.2
BATT_MEAS: JP-CP.5, R3-11P.1, R4-11P.2
CHECK_HDD: R1-11P7.2, R1-11P9.1, TERMINALBLOCK.1
CMP_ARM_DIV: R1.2, R2.1, U7-P1.5 (2IN+)
CMP_LDO_IN: R1-11P.1, R2-11P.2, U7-P.3 (1IN+), U7-P.5 (2IN+), U8-P.3 (1IN+), U8-P.5 (2IN+)
CMP_LDO_OUT_1: Q1-5P.2 (G1), R2-5P.2, U7-P.1 (1OUT)
CMP_LDO_OUT_2: Q1-5P.4 (G2), R6-5P.2, U7-P.7 (2OUT)
CMP_LDO_OUT_3: Q1-6P.2 (G1), R2-6P.2, U8-P.1 (1OUT)
CMP_LDO_OUT_4: Q1-6P.4 (G2), R6-6P.2, U8-P.7 (2OUT)
CMP_RAIL: R3-9P.1, R4-9P.2, U7-P.2 (1IN-), U7-P.6 (2IN-), U8-P.2 (1IN-), U8-P.6 (2IN-)
CTS: J1-9P.13, J1-CP.4
D1-1P_R1-1P: D1-1P.C, R1-1P.1
FET_A: J2-P.2, Q1-5P.7 (D1_1), Q1-5P.8 (D1_2), R4-5P.2, U8-P1.3 (1IN+)
FET_B: J2-P.4, Q1-5P.5 (D2_1), Q1-5P.6 (D2_2), R8-5P.2, U8-P1.5 (2IN+)
FET_C: J2-P.6, Q1-6P.7 (D1_1), Q1-6P.8 (D1_2), R4-6P.2, U8-P2.3 (1IN+)
FET_D: J2-P.8, Q1-6P.5 (D2_1), Q1-6P.6 (D2_2), R8-6P.2, U8-P2.5 (2IN+)
FIRE_A: J2-CP.1, R1-5P.2, R2-5P.1
FIRE_B: J2-CP.2, R5-5P.2, R6-5P.1
FIRE_C: J2-CP.3, R1-6P.2, R2-6P.1
FIRE_D: J2-CP.4, R5-6P.2, R6-6P.1
GND: 1S_LIPO1.2, C1-1P.2, C1-11P.2, C2-1P.2, C2-9P.2, C3-9P.2, C4-9P.2, C4-9P2.2, C4-9P3.2, CIN.2, COUT.2, D1-1P2.C, D1-1P4.C, D1-1P5.C, IC1.1 (GND), J1-9P.15, JP-CP.3, Q1-5P.1 (S1), Q1-5P.3 (S2), Q1-6P.1 (S1), Q1-6P.3 (S2), R1.1, R2-1P.1, R2-9P.1, R2-11P.1, R3-11P.2, R4-5P.1, R4-6P.1, R4-9P.1, R8-5P.1, R8-6P.1, R-EXT.1, U1-P.2 (VSS), U7-P.4 (GND), U7-P1.4 (GND), U8-P.4 (GND), U8-P1.4 (GND), U8-P2.4 (GND), U9-P.2 (GND), U$1.3 (GND), U$1.5 (SD), U$1.6 (GND), U$3.3 (E), U$4.3 (E), U$5.3 (E), U$6.3 (E), U$7.3 (E), U$10.3 (E), U$11.3 (E), U$13.3 (E), U$14.3 (E), U$15.3 (E), U$16.3 (E), U$17.3 (E), U$18.3 (E), U$19.8 (VSS), U$20.1 (GND), U$20.21 (!OE!(ED2)), U$21.8 (VSS)
IO_CLK: U$20.3 (CLK)
IO_LE: U$20.4 (LE(ED1))
IO_SDI: U$20.2 (SDI)
LED_SINK_0: D0.C, U$20.5 (OUT0)
LED_SINK_1: D1.C, U$20.6 (OUT1)
LED_SINK_2: D2.C, U$19.14 (I6), U$20.7 (OUT2)
LED_SINK_3: D3.C, U$19.3 (I1), U$20.8 (OUT3)
LED_SINK_4: D4.C, U$19.5 (I2), U$20.9 (OUT4)
LED_SINK_5: D5.C, U$19.11 (I5), U$20.10 (OUT5)
LED_SINK_6: D6.C, U$19.7 (I3), U$20.11 (OUT6)
LED_SINK_7: D7.C, U$19.9 (I4), U$20.12 (OUT7)
LED_SINK_8: D8.C, U$20.13 (OUT8), U$21.9 (I4)
LED_SINK_9: D9.C, U$20.14 (OUT9), U$21.7 (I3)
LED_SINK_10: D10.C, U$20.15 (OUT10), U$21.11 (I5)
LED_SINK_11: D11.C, U$20.16 (OUT11), U$21.5 (I2)
LED_SINK_12: D12.C, U$20.17 (OUT12), U$21.14 (I6)
LED_SINK_13: D13.C, U$20.18 (OUT13), U$21.3 (I1)
LED_SINK_14: D14.C, U$20.19 (OUT14)
LED_SINK_15: D15.C, U$20.20 (OUT15)
MASTER_RX-2: J1-9P.7, J1-CP.2
MASTER_TX-2: J1-9P.9, J1-CP.3
unnamed: 1S_LIPO.2, 1S_LIPO1.1
unnamed: R1-11P8.1, U$4.1 (B)
unnamed: R1-11P1.1, U$8.1 (B)
unnamed: D1-1P3.C, U$7.2 (C)
unnamed: R6.2, R7.1, U$10.2 (C)
unnamed: R6.1, U$7.1 (B)
unnamed: P-CHANNEL_MOSFET1.3 (G), R1-11P5.2, U$3.2 (C)
unnamed: R1-11P4.2, U$3.1 (B)
unnamed: R1-11P4.1, R1-11P8.2, R1-11P13.1, U7-P1.7 (2OUT), U$6.2 (C)
unnamed: R5.1, U$5.1 (B)
unnamed: R1-11P7.1, U$6.1 (B)
unnamed: R1-11P2.1, R1-11P3.1, U$12.3 (C)
unnamed: R1-11P9.2, U$10.1 (B), U$11.1 (B)
unnamed: R3.1, U$5.2 (C)
unnamed: D1-1P2.A, R1-11P2.2
unnamed: D1-1P3.A, R1-11P10.1
unnamed: R12.1, U$4.2 (C), U$13.1 (B)
unnamed: D1-1P6.A, R1-11P11.1
unnamed: R9.1, U$12.1 (B)
unnamed: R1-11P12.1, U$8.3 (C)
unnamed: D1-1P4.A, R1-11P12.2
unnamed: R9.2, U$11.2 (C)
unnamed: R4.1, U$9.1 (B)
unnamed: D1-1P5.A, R1-11P3.2
unnamed: IC1.4 (/RES), R11.1, U$13.2 (C)
unnamed: R13.1, U$14.1 (B)
unnamed: C4-9P2.1, IC1.5 (CON)
unnamed: C4-9P3.1, IC1.2 (TRI), IC1.6 (TRE), R8.2
unnamed: IC1.7 (DIS), R8.1, R10.2
unnamed: IC1.3 (OUT), R13.2
unnamed: D1-1P7.A, R1-11P6.1
unnamed: D1-1P6.C, D1-1P7.C, U$14.2 (C)
unnamed: R5-5P.1, U$15.1 (B)
unnamed: D1-1P8.C, U$16.2 (C)
unnamed: D1-1P9.A, R1-11P15.1
unnamed: D1-1P9.C, U$15.2 (C)
unnamed: D1-1P8.A, R1-11P14.1
unnamed: R1-5P.1, U$16.1 (B)
unnamed: R1-6P.1, U$17.1 (B)
unnamed: R5-6P.1, U$18.1 (B)
unnamed: D1-1P10.C, U$17.2 (C)
unnamed: D1-1P10.A, R1-11P16.1
unnamed: D1-1P11.C, U$18.2 (C)
unnamed: D1-1P11.A, R1-11P17.1
unnamed: D7.A, SW2.10
unnamed: R-EXT.2, U$20.23 (R-EXT)
unnamed: D3.A, SW2.6
unnamed: D4.A, SW2.7
unnamed: D5.A, SW2.8
unnamed: D6.A, SW2.9
unnamed: D2.A, SW3.4
unnamed: D12.A, SW1.10
unnamed: D11.A, SW1.9
unnamed: D10.A, SW1.8
unnamed: D9.A, SW1.7
unnamed: D8.A, SW1.6
unnamed: D13.A, SW3.3
RTS: J1-9P.5, J1-CP.1
SENSE_A: J3-CP.1, R3-11P1.1, U8-P1.1 (1OUT)
SENSE_B: J3-CP.2, R3-11P2.1, U8-P1.7 (2OUT)
SENSE_C: J3-CP.3, R3-11P3.1, U8-P2.1 (1OUT)
SENSE_D: J3-CP.4, R3-11P4.1, U8-P2.7 (2OUT)
SWITCH_PLEX_READ: U$19.2 (O1), U$19.4 (O2), U$19.6 (O3), U$19.10 (O4), U$19.12 (O5), U$19.16 (O6), U$21.2 (O1), U$21.4 (O2), U$21.6 (O3), U$21.10 (O4), U$21.12 (O5), U$21.16 (O6)
U1P-PROG: R2-1P.2, U1-P.5 (PROG)
U1P-STAT: R1-1P.2, U1-P.1 (STAT)
U9P-FB: C1-9P.2, C2-9P.1, R1-9P.1, R2-9P.2, U9-P.4 (FB)
U9P-SW: L1-9P.1, U9-P.5 (SW)
VBAT: 1S_LIPO.1, C2-1P.1, R5-11P.1, S1-P.P, U1-P.3 (VBAT)
VBAT_AFTER_ARMING: J2-P.1, J2-P.3, J2-P.5, J2-P.7, P-CHANNEL_MOSFET1.1 (D), P-CHANNEL_MOSFET1.2 (D), P-CHANNEL_MOSFET1.5 (D), P-CHANNEL_MOSFET1.6 (D)
VBAT_AFTER_SWITCH: CIN.1, D1-11P.2 (A), P-CHANNEL_MOSFET1.4 (S), R1-11P5.1, R4-11P.1, R5-11P.2, S1-P.S, U$1.1 (VIN)
VUSB: C1-1P.1, D1-1P.A, JP-CP.4, U1-P.4 (VDD)
V_LDO_IN: C1-11P.1, D1-11P.1 (K), R1-11P.2

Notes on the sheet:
Power Systems and Deployment
Deployment (Q5-P)
R1-5P: 3.3K R2-5P: 1K R3-5P: 100K R4-5P: 27K R5-5P: 3.3K R6-5P: 1K R7-5P: 100K R8-5P: 27K Q1-5P: TBD
1725711 - 8 Pin Terminal Block (3P)
MCP73831 - Charge Managment (U1-P)
D1-1P: TBD R1-1P: 1K R2-1P: 2K C1-1P: 4.7uF C2-1P: 4.7uF
LM3671-ADJ - Step Down (U9-P)
R1-9P: 562k R2-9P: 100k R3-9P: 10k R4-9P: 9.09k C1-9P: 33pF C2-9P: 6.8pF C3-9P: 4.7pF C4-9P: 10uF L1-9P: 2.2uH
LM293DR - LDO Comparator (U7-P)
VBAT to V_LDO_IN and CMP_LDO_IN (11P)
D1-11P: TBD R1-11P: 10k R2-11P: 8.0k R3-11P: 100k R4-11P: 100k R5-11P: 0k C1-11P: 47uF
Deployment (Q6-P)
R1-6P: 3.3K R2-6P: 1K R3-6P: 100K R4-6P: 27K R5-6P: 3.3K R6-6P: 1K R7-6P: 100K R8-6P: 27K Q1-6P: TBD
LM293DR - LDO Comparator (U8-P)
1725711 - 8 Pin Terminal Block (Radio) (9P)
Central
Power
Sensors
Board Interfaces
[R4/(R4+R3)]*[(R1+R2)/R2]*3.3V = Stop Deploy
LM293DR - Sense Comparator (U8-P)
(Digital Output)
Hardware Disable LED
Arming LED
Armed LED
Blinks when no HDD and arming after arming time
Hardware Deployment Disable (HDD)
Short terminal block to disable all deployment
Arming time: t = RC*ln[(R1+R2)/(R1)] t ≈ 9.5 sec = (82kΩ)(100uF)*ln(32kΩ/10kΩ)
(ADC input)
(Digital input)
Safe LED
To GPIOs



Board: 2 copper layers, 145 parts (4 on the bottom side), 114 nets.

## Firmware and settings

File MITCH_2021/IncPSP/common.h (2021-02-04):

/*
 * common.h
 *
 *  Created on: Dec 15, 2020
 *      Author: vishv
 */

#ifndef COMMON_H_
#define COMMON_H_

#include <stdint.h>
#include <stdbool.h>
#include <stdio.h>
#include <stdlib.h>
#include <string.h>
#include <assert.h>
#include <math.h>

#include "main.h" // NDEBUG is now defined in main.h

#ifdef NDEBUG
#include "cmsis_os.h"
#include "stm32f4xx_hal.h"
#include "gpio.h"
#include "retarget.h"
#endif


/* User-defined Macros */
#define MIN(A, B) ( ((A)<(B)) ? (A) : (B))
#define MAX(A, B) ( ((A)>(B)) ? (A) : (B))
#define getBit(A, X) ((((A >> X) & 0x01) == 0x01) ? (0x01) : (0x00))
#define setBit(A, X, V) (A & ~((0x01 << X) | (V << X)))


/* User-defined Constants*/

#define MAX_NMEA (80)
#define DEFAULT_DAQ_SCALER (10)
#define MAX_TRANSMISSION_SIZE (100)
#define TAN_THETA_SQUARED (32) // Theta is about 80 degrees

#define DEFAULT_TAKE_DELAY (50)

#define ALTITUDE_LIST_SIZE (20)
#define ALA_LIST_SIZE (40)
#define STATIC_ORIENTATION_LIST_SIZE (20)

// Nominal mode flow
#define PRELAUNCH (1)
#define LAUNCH (2)
#define ASCENT (3)
#define DESCENT_DROGUE (4)
#define DESCENT_MAIN (5)
#define TOUCHDOWN (6)
#define PROGRAM_END (7)


// Sensor Defines



typedef enum {
	TASK_UPDATE = 0,
	SETUP_WARNING = 1
} Message_ID;

// Function returns
#define SUCCESSFUL_RETURN (0)



/* User typedef */

typedef uint8_t ui8;
typedef uint16_t ui16;
typedef uint32_t ui32;
typedef int16_t i16;
typedef int32_t i32;

/* Typedef structs and types */

typedef struct altitudeNode altitudeNode_t;
typedef struct alaNode alaNode_t;
typedef struct staticOrientationNode staticOrientationNode_t;


typedef struct daqStatusData {
	ui32 timeStamp;
	bool daqScalingEnabled;
	bool gpsNominal;
	bool bmpNominal;
	bool imuNominal;
	bool alaNominal;
	bool hasUpdate;
	bool lock;
} daqStatusData_t;

typedef struct daqScalingData {
	bool enableDaqScaling;
	bool hasUpdate;
	bool lock;
} daqScalingData_t;

typedef struct gpsData {
	ui32 timeStamp;
	char nmeaGGA[MAX_NMEA];
	char nmeaRMC[MAX_NMEA];
	ui8 fix;
	float alt;
	float speed;
	int utc;
	bool hasUpdate;
	bool lock;
} gpsData_t;


typedef struct bmpData {
	ui32 timeStamp;
	i32 pressure;     // MIN: 1000, MAX: 120000, VALUE: 110002 = 1100.02 mbar
	i32 temperature;  // MIN:-4000, MAX: 8500,   VALUE: 2000 = 20.00 degC
	bool hasUpdate;
	bool lock;
} bmpData_t;


typedef struct imuData {
	ui32 timeStamp;
	i16 accel_xout;
	i16 accel_yout;
	i16 accel_zout;
	i16 gyro_xout;
	i16 gyro_yout;
	i16 gyro_zout;
	i16 mag_xout;
	i16 mag_yout;
	i16 mag_zout;
	float alaZ;
	bool hasUpdate;
	bool lock;

} imuData_t;

typedef struct processedData {
	ui32 timeStamp;

} processedData_t;

typedef struct monitoringData {
	ui32 timeStamp;
	float batteryVoltage;
	bool continuity[4];
	bool buttonState;
	bool hardwareDeploymentDisable;
	bool hasUpdate;
	bool lock;

} monitoringData_t;

typedef struct transmissionData {
	float altitude;
	float accelerationDataX;
	float accelerationDataY;
	float accelerationDataZ;
	float trajectoryDataX;
	float trajectoryDataY;
	float trajectoryDataZ;
	float resolvedOrientationX;
	float resolvedOrientationY;
	float resolvedOrientationZ;
	float rawData;
	bool lock;
	bool hasUpdate;
} transmissionData_t;

/* Node structures */

typedef struct altitudeNode {
	float altitude;
	bool lock;
	altitudeNode_t *nextNode;
} altitudeNode_t;

typedef struct alaNode {
	float gForce;
	bool lock;
	alaNode_t *nextNode;
} alaNode_t;

typedef struct staticOrientationNode {
	float staticOrientation;
	bool lock;
	staticOrientationNode_t *nextNode;
} staticOrientationNode_t;

/* Extern variable definitions */

extern volatile daqStatusData_t g_daqStatusData;
extern volatile daqScalingData_t g_daqScalingData;
extern volatile gpsData_t g_gpsData;
extern volatile bmpData_t g_bmpData;
extern volatile imuData_t g_imuData;
extern volatile monitoringData_t g_monitoringData;
extern volatile transmissionData_t g_transmissionData;

extern volatile ui8 g_currentNominalMode;
extern volatile ui8 g_currentContingency;
extern volatile ui32 g_launchTime;

extern altitudeNode_t *g_newAltitudeNode;
extern alaNode_t *g_newALANode;
extern staticOrientationNode_t *g_newStaticOrientationNode;

/* Common Function Prototypes */

ui32 getTimeStamp(void );
void retryTakeDelay(int );

#ifdef NDEBUG

#endif

altitudeNode_t *createAltitudeList(ui8 );
alaNode_t *createALAList(ui8 );
staticOrientationNode_t *createStaticOrientationList(ui8 );
int setupLinkedLists();

int freeAltitudeList(altitudeNode_t *);
int freeALAList(alaNode_t *);
int freeStaticOrientationList(staticOrientationNode_t *);
int freeAllLists();

int insertNewAltitude(float );
int insertNewALA(float );
int insertNewStaticOrientation(float );

float calcAvgAlt();

//void notify(Message_ID message, Device_ID device);




#endif /* COMMON_H_ */

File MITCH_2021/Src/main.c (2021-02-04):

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
/* Includes ------------------------------------------------------------------*/
#include "main.h"
#include "cmsis_os.h"

/* USER CODE BEGIN Includes */
#include "task.h"
/* User-defined libraries */

#include <stdbool.h>
#include <stdint.h>

#include "../IncPSP/acquisition.h"
#include "../IncPSP/common.h"
#include "../IncPSP/controlLogic.h"
#include "../IncPSP/monitoring.h"
#include "../IncPSP/processing.h"
#include "../IncPSP/storage.h"
#include "../IncPSP/transmission.h"

/* USER CODE END Includes */

ADC_HandleTypeDef hadc1;
DMA_HandleTypeDef hdma_adc1;

I2C_HandleTypeDef hi2c3;

SPI_HandleTypeDef hspi1;
SPI_HandleTypeDef hspi3;
DMA_HandleTypeDef hdma_spi1_rx;

UART_HandleTypeDef huart2;
UART_HandleTypeDef huart6;

osThreadId ControlLogicHandle;
uint32_t ControlLogicBuffer[ 128 ];
osStaticThreadDef_t ControlLogicControlBlock;
osThreadId AcquisitionHandle;
uint32_t AcquisitionBuffer[ 128 ];
osStaticThreadDef_t AcquisitionControlBlock;
osThreadId ProcessingHandle;
uint32_t ProcessingBuffer[ 128 ];
osStaticThreadDef_t ProcessingControlBlock;
osThreadId MonitoringHandle;
uint32_t MonitoringBuffer[ 128 ];
osStaticThreadDef_t MonitoringControlBlock;
/* USER CODE BEGIN PV */
led_t U1S_CHECK_Led;
led_t U2S_CHECK_Led;
led_t U3S_CHECK_Led;
led_t U4S_CHECK_Led;

led_t SENSOR_NOMINAL_Led;
led_t SENSOR_ERROR_Led;
/* USER CODE END PV */

void SystemClock_Config(void);
static void MX_GPIO_Init(void);
static void MX_DMA_Init(void);
static void MX_I2C3_Init(void);
static void MX_SPI1_Init(void);
static void MX_SPI3_Init(void);
static void MX_USART2_UART_Init(void);
static void MX_USART6_UART_Init(void);
static void MX_USB_OTG_FS_USB_Init(void);
static void MX_ADC1_Init(void);
void startControlLogic(void const * argument);
void startAcquisition(void const * argument);
void startProcessing(void const * argument);
void startMonitoring(void const * argument);

/**
  * @brief  The application entry point.
  * @retval int
  */
int main(void)
{
  /* USER CODE BEGIN 1 */
	U1S_CHECK_Led = newPinLed(U1S_CHECK_GPIO_Port, U1S_CHECK_Pin);
	U2S_CHECK_Led = newPinLed(U2S_CHECK_GPIO_Port, U1S_CHECK_Pin);
	U3S_CHECK_Led = newPinLed(U3S_CHECK_GPIO_Port, U1S_CHECK_Pin);
	U4S_CHECK_Led = newPinLed(U4S_CHECK_GPIO_Port, U4S_CHECK_Pin);

	SENSOR_NOMINAL_Led = newPinLed(SENSOR_NOMINAL_GPIO_Port, SENSOR_NOMINAL_Pin);
	SENSOR_ERROR_Led = newPinLed(SENSOR_ERROR_GPIO_Port, SENSOR_ERROR_Pin);
  /* USER CODE END 1 */

  /* MCU Configuration--------------------------------------------------------*/

  /* Reset of all peripherals, Initializes the Flash interface and the Systick. */
  HAL_Init();

  /* Configure the system clock */
  SystemClock_Config();

  /* Initialize all configured peripherals */
  MX_GPIO_Init();
  MX_DMA_Init();
  MX_I2C3_Init();
  MX_SPI1_Init();
  MX_SPI3_Init();
  MX_USART2_UART_Init();
  MX_USART6_UART_Init();
  MX_USB_OTG_FS_USB_Init();
  MX_ADC1_Init();
  /* USER CODE BEGIN 2 */


  setup_A();
  setup_M();

  /* USER CODE END 2 */

  /* USER CODE BEGIN RTOS_MUTEX */
  /* add mutexes, ... */
  /* USER CODE END RTOS_MUTEX */

  /* USER CODE BEGIN RTOS_SEMAPHORES */
  /* add semaphores, ... */
  /* USER CODE END RTOS_SEMAPHORES */

  /* USER CODE BEGIN RTOS_TIMERS */
  /* start timers, add new ones, ... */
  /* USER CODE END RTOS_TIMERS */

  /* USER CODE BEGIN RTOS_QUEUES */
  /* add queues, ... */
  /* USER CODE END RTOS_QUEUES */

  /* Create the thread(s) */
  /* definition and creation of ControlLogic */
  osThreadStaticDef(ControlLogic, startControlLogic, osPriorityNormal, 0, 128, ControlLogicBuffer, &ControlLogicControlBlock);
  ControlLogicHandle = osThreadCreate(osThread(ControlLogic), NULL);

  /* definition and creation of Acquisition */
  osThreadStaticDef(Acquisition, startAcquisition, osPriorityRealtime, 0, 128, AcquisitionBuffer, &AcquisitionControlBlock);
  AcquisitionHandle = osThreadCreate(osThread(Acquisition), NULL);

  /* definition and creation of Processing */
  osThreadStaticDef(Processing, startProcessing, osPriorityNormal, 0, 128, ProcessingBuffer, &ProcessingControlBlock);
  ProcessingHandle = osThreadCreate(osThread(Processing), NULL);

  /* definition and creation of Monitoring */
  osThreadStaticDef(Monitoring, startMonitoring, osPriorityLow, 0, 128, MonitoringBuffer, &MonitoringControlBlock);
  MonitoringHandle = osThreadCreate(osThread(Monitoring), NULL);

  /* USER CODE BEGIN RTOS_THREADS */
  /* add threads, ... */
  /* USER CODE END RTOS_THREADS */

  /* Start scheduler */
  osKernelStart();

  /* We should never get here as control is now taken by the scheduler */
  /* Infinite loop */
  /* USER CODE BEGIN WHILE */
  while (1)
  {
    /* USER CODE END WHILE */

    /* USER CODE BEGIN 3 */
  }
  /* USER CODE END 3 */
}

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
/* USER CODE BEGIN Header_startControlLogic */
/**
* @brief Function implementing the ControlLogic thread.
* @param argument: Not used
* @retval None
*/
/* USER CODE END Header_startControlLogic */
void startControlLogic(void const * argument)
{
  /* USER CODE BEGIN 5 */
	static TickType_t time_init = 0;
  /* Infinite loop */
	while(ENABLE_CONTROL_LOGIC) {

		vTaskDelayUntil(&time_init, CONTROL_LOGIC_TASK_DELAY);
	}
  /* USER CODE END 5 */
}

/* USER CODE BEGIN Header_startAcquisition */
/**
* @brief Function implementing the Acquisition thread.
* @param argument: Not used
* @retval None
*/
/* USER CODE END Header_startAcquisition */
void startAcquisition(void const * argument)
{
  /* USER CODE BEGIN startAcquisition */
	static TickType_t time_init = 0;

  /* Infinite loop */
	while(ENABLE_ACQUISITION) {
		switch(loop_A()) {
		case 1: vTaskDelayUntil(&time_init, ACQUISITION_TASK_DELAY1);
				break;

		case 2: vTaskDelayUntil(&time_init, ACQUISITION_TASK_DELAY2);
				break;

		default:vTaskDelayUntil(&time_init, ACQUISITION_TASK_DELAY0);
				break;
		}
	}

  /* USER CODE END startAcquisition */
}

/* USER CODE BEGIN Header_startProcessing */
/**
* @brief Function implementing the Processing thread.
* @param argument: Not used
* @retval None
*/
/* USER CODE END Header_startProcessing */
void startProcessing(void const * argument)
{
  /* USER CODE BEGIN startProcessing */
	static TickType_t time_init = 0;
  /* Infinite loop */
	while(ENABLE_PROCESSING) {

		vTaskDelayUntil(&time_init, PROCESSING_TASK_DELAY);
	}
  /* USER CODE END startProcessing */
}

/* USER CODE BEGIN Header_startMonitoring */
/**
* @brief Function implementing the Monitoring thread.
* @param argument: Not used
* @retval None
*/
/* USER CODE END Header_startMonitoring */
void startMonitoring(void const * argument)
{
  /* USER CODE BEGIN startMonitoring */
	static TickType_t time_init = 0;
  /* Infinite loop */
	while(ENABLE_MONITORING) {
		loop_M();
		vTaskDelayUntil(&time_init, MONITORING_TASK_DELAY);
	}
  /* USER CODE END startMonitoring */
}

 /**
  * @brief  Period elapsed callback in non blocking mode
  * @note   This function is called  when TIM1 interrupt took place, inside
  * HAL_TIM_IRQHandler(). It makes a direct call to HAL_IncTick() to increment
  * a global variable "uwTick" used as application time base.
  * @param  htim : TIM handle
  * @retval None
  */
void HAL_TIM_PeriodElapsedCallback(TIM_HandleTypeDef *htim)
{
  if (htim->Instance == TIM1) {
    HAL_IncTick();
  }
}

/**
  * @brief  This function is executed in case of error occurrence.
  * @retval None
  */
void Error_Handler(void)
{
  /* USER CODE BEGIN Error_Handler_Debug */
  /* User can add his own implementation to report the HAL error return state */

  /* USER CODE END Error_Handler_Debug */
}

#ifdef  USE_FULL_ASSERT
/**
  * @brief  Reports the name of the source file and the source line number
  *         where the assert_param error has occurred.
  * @param  file: pointer to the source file name
  * @param  line: assert_param error line source number
  * @retval None
  */
void assert_failed(uint8_t *file, uint32_t line)
{
  /* USER CODE BEGIN 6 */
  /* User can add his own implementation to report the file name and line number,
     tex: printf("Wrong parameters value: file %s on line %d\r\n", file, line) */
  /* USER CODE END 6 */
}
#endif /* USE_FULL_ASSERT */

/************************ (C) COPYRIGHT STMicroelectronics *****END OF FILE****/

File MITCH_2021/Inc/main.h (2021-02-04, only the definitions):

#define BUZZER_OUT_Pin GPIO_PIN_2
#define BUZZER_OUT_GPIO_Port GPIOE
#define FIRE_A_Pin GPIO_PIN_1
#define FIRE_A_GPIO_Port GPIOF
#define FIRE_B_Pin GPIO_PIN_2
#define FIRE_B_GPIO_Port GPIOF
#define FIRE_C_Pin GPIO_PIN_3
#define FIRE_C_GPIO_Port GPIOF
#define FIRE_D_Pin GPIO_PIN_4
#define FIRE_D_GPIO_Port GPIOF
#define SENSE_A_Pin GPIO_PIN_6
#define SENSE_A_GPIO_Port GPIOF
#define SENSE_B_Pin GPIO_PIN_7
#define SENSE_B_GPIO_Port GPIOF
#define SENSE_C_Pin GPIO_PIN_8
#define SENSE_C_GPIO_Port GPIOF
#define SENSE_D_Pin GPIO_PIN_9
#define SENSE_D_GPIO_Port GPIOF
#define CS1_Pin GPIO_PIN_4
#define CS1_GPIO_Port GPIOC
#define CS2_Pin GPIO_PIN_5
#define CS2_GPIO_Port GPIOC
#define ACCEL_ANALOG_Pin GPIO_PIN_0
#define ACCEL_ANALOG_GPIO_Port GPIOB
#define BATT_MEAS_Pin GPIO_PIN_1
#define BATT_MEAS_GPIO_Port GPIOB
#define ARMED_LED_Pin GPIO_PIN_13
#define ARMED_LED_GPIO_Port GPIOF
#define CENTRAL_NOMINAL_Pin GPIO_PIN_14
#define CENTRAL_NOMINAL_GPIO_Port GPIOF
#define CENTRAL_ERROR_Pin GPIO_PIN_15
#define CENTRAL_ERROR_GPIO_Port GPIOF
#define DROGUE_LED_Pin GPIO_PIN_0
#define DROGUE_LED_GPIO_Port GPIOG
#define MAIN_LED_Pin GPIO_PIN_1
#define MAIN_LED_GPIO_Port GPIOG
#define STORAGE_ERROR_Pin GPIO_PIN_7
#define STORAGE_ERROR_GPIO_Port GPIOE
#define ADC_ERROR_Pin GPIO_PIN_8
#define ADC_ERROR_GPIO_Port GPIOE
#define SENSOR_NOMINAL_Pin GPIO_PIN_10
#define SENSOR_NOMINAL_GPIO_Port GPIOE
#define SENSOR_ERROR_Pin GPIO_PIN_11
#define SENSOR_ERROR_GPIO_Port GPIOE
#define U1S_CHECK_Pin GPIO_PIN_12
#define U1S_CHECK_GPIO_Port GPIOE
#define U2S_CHECK_Pin GPIO_PIN_13
#define U2S_CHECK_GPIO_Port GPIOE
#define U3S_CHECK_Pin GPIO_PIN_14
#define U3S_CHECK_GPIO_Port GPIOE
#define U4S_CHECK_Pin GPIO_PIN_15
#define U4S_CHECK_GPIO_Port GPIOE
#define US2_ST_Pin GPIO_PIN_10
#define US2_ST_GPIO_Port GPIOB
#define US2_STATUS_Pin GPIO_PIN_11
#define US2_STATUS_GPIO_Port GPIOB
#define CHECK_HARDWARE_DEPLOYMENT_DISABLE_Pin GPIO_PIN_12
#define CHECK_HARDWARE_DEPLOYMENT_DISABLE_GPIO_Port GPIOB
#define DISARM_INPUT_Pin GPIO_PIN_4
#define DISARM_INPUT_GPIO_Port GPIOG
#define ADC_ALERT_Pin GPIO_PIN_8
#define ADC_ALERT_GPIO_Port GPIOC
#define CS3_Pin GPIO_PIN_0
#define CS3_GPIO_Port GPIOD
#define WP_Pin GPIO_PIN_1
#define WP_GPIO_Port GPIOD
#define HOLD_Pin GPIO_PIN_2
#define HOLD_GPIO_Port GPIOD
#define GPS_FREQ (1)        //   1 Hz
#define BMP_MULTIPLIER (10) //  10 Hz
#define IMU_MULTIPLIER (10) // 100 Hz
#define ACQUISITION_TASK_RATE0  (GPS_FREQ)
#define ACQUISITION_TASK_RATE1  (GPS_FREQ * BMP_MULTIPLIER)
#define ACQUISITION_TASK_RATE2  (GPS_FREQ * BMP_MULTIPLIER * IMU_MULTIPLIER)
#define CONTROL_LOGIC_TASK_RATE (1)   // TODO: Determine optimal Control Logic Task Rate (currently 1 Hz)
#define MONITORING_TASK_RATE    (1)   // TODO: Determine optimal Monitoring Task Rate (currently 1 Hz)
#define PROCESSING_TASK_RATE    (125) // TODO: Determine optimal Processing Task Rate (currently 125 Hz)
#define ACQUISITION_TASK_DELAY0  (1000 / ACQUISITION_TASK_RATE0 / portTICK_RATE_MS)
#define ACQUISITION_TASK_DELAY1  (1000 / ACQUISITION_TASK_RATE1 / portTICK_RATE_MS)
#define ACQUISITION_TASK_DELAY2  (1000 / ACQUISITION_TASK_RATE2 / portTICK_RATE_MS)
#define CONTROL_LOGIC_TASK_DELAY (1000 / CONTROL_LOGIC_TASK_RATE / portTICK_RATE_MS)
#define MONITORING_TASK_DELAY    (1000 / MONITORING_TASK_RATE / portTICK_RATE_MS)
#define PROCESSING_TASK_DELAY    (1000 / PROCESSING_TASK_RATE / portTICK_RATE_MS)
#define ENABLE_CONTROL_LOGIC (1)
#define ENABLE_ACQUISITION (1)
#define ENABLE_MONITORING (1)
#define ENABLE_PROCESSING (1)

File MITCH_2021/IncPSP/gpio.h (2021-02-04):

/*
 * gpio.h
 *
 *  Created on: Jan 26, 2021
 *      Author: Jeff
 */

#ifndef GPIO_H_
#define GPIO_H_
#include "genericInterface.h"

#ifdef LD2_Pin
void toggleLed();
#endif

// GPIO Setup
#ifdef NDEBUG
// GPIO Simulation Constants
	#define FAKE_GPIO ((uint16_t)-1)

	#ifndef SENSE_A_Pin
		#define SENSE_A_Pin (FAKE_GPIO)
		#define SENSE_A_GPIO_Port (0)
	#endif

	#ifndef SENSE_B_Pin
		#define SENSE_B_Pin (FAKE_GPIO)
		#define SENSE_B_GPIO_Port (0)
	#endif

	#ifndef SENSE_C_Pin
		#define SENSE_C_Pin (FAKE_GPIO)
		#define SENSE_C_GPIO_Port (0)
	#endif

	#ifndef SENSE_D_Pin
		#define SENSE_D_Pin (FAKE_GPIO)
		#define SENSE_D_GPIO_Port (0)
	#endif

	#ifndef DISARM_INPUT_Pin
		#define DISARM_INPUT_Pin (FAKE_GPIO)
		#define DISARM_INPUT_GPIO_Port (0)
	#endif

	#ifndef CHECK_HARDWARE_DEPLOYMENT_DISABLE_Pin
		#define CHECK_HARDWARE_DEPLOYMENT_DISABLE_Pin (FAKE_GPIO)
		#define CHECK_HARDWARE_DEPLOYMENT_DISABLE_GPIO_Port (0)
	#endif

	#ifndef U1S_CHECK_Pin
		#define U1S_CHECK_Pin (FAKE_GPIO)
		#define U1S_CHECK_GPIO_Port (0)
	#endif

	#ifndef U2S_CHECK_Pin
		#define U2S_CHECK_Pin (FAKE_GPIO)
		#define U2S_CHECK_GPIO_Port (0)
	#endif

	#ifndef U3S_CHECK_Pin
		#define U3S_CHECK_Pin (FAKE_GPIO)
		#define U3S_CHECK_GPIO_Port (0)
	#endif

	#ifndef U4S_CHECK_Pin
		#define U4S_CHECK_Pin (FAKE_GPIO)
		#define U4S_CHECK_GPIO_Port (0)
	#endif

	#ifndef SENSOR_NOMINAL_Pin
		#define SENSOR_NOMINAL_Pin (FAKE_GPIO)
		#define SENSOR_NOMINAL_GPIO_Port (0)
	#endif

	#ifndef SENSOR_ERROR_Pin
		#define SENSOR_ERROR_Pin (FAKE_GPIO)
		#define SENSOR_ERROR_GPIO_Port (0)
	#endif

	#ifndef CS1_Pin
		#define CS1_Pin (FAKE_GPIO)
		#define CS1_GPIO_Port (0)
	#endif

	#ifndef CS2_Pin
		#define CS2_Pin (FAKE_GPIO)
		#define CS2_GPIO_Port (0)
	#endif

	#ifndef CS3_Pin
		#define CS3_Pin (FAKE_GPIO)
		#define CS3_GPIO_Port (0)
	#endif

#ifndef NAND_CS_Pin
#define NAND_CS_Pin (FAKE_GPIO)
#define NAND_CS_GPIO_Port (0)
#endif




#endif



#endif /* GPIO_H_ */

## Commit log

2020-12-13 Setup Libraries
    fixed mess
    [acquisition.c, main.c, monitoring.c]
2020-12-13 Corrected Spelling Mistake
    Montoring -> Monitoring
    Also generated:
    \AnR\MITCH_2021\Drivers\CMSIS\Device\ST\STM32F4xx\Source\Templates\system_stm32f4xx.c
    (We don't know what it does) ¯\_(ツ)_/¯
    [MITCH_2021.ioc, main.c]
2020-12-16 Expanded common.h
    Added/Improved definitions for
    - daqStatusData
    - gpsData
    - bmpData
    - imuData
2020-12-23 Updated Functions
    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
    [acquisition.c, common.h]
2020-12-24 Created Transmission Prototype Functions
2020-12-24 Created Acquisition Prototype Functions
2020-12-24 Monitoring function prototypes
2020-12-24 controlLogic Function Prototypes
2020-12-24 Storage function prototypes
    Added storage function prototypes
    Also included "common.h" to all the tasks but processing bc that still isn't figured out so I didn't want to touch it
    [common.h]
2020-12-29 Shortened variable names
    Consolidated byte into uint8_t
    Shortened uint8_t to u8
    Shortened uint16_t to u16
    Shortened uint32_t to u32
    [acquisition.c, common.h]
2020-12-29 Processing function prototypes
2020-12-29 Updated constants and asserts
    Included nominal mode flow constants, defined extern mode flow variables, added asserts and NDEBUG logic
2020-12-29 Fixed logic -- Stable build
    [common.h]
2020-12-31 Created print() macro for debug only
    Also corrected documentation for _splitNmea
    [acquisition.c, common.h]
2020-12-31 Implemented debug sensor setup functions
2020-12-31 Added second print macro without parameters
2021-01-01 Implemented txt file sensor simulation
2021-01-01 Expanded Acquisition flow chart implementation
2021-01-02 Encapsulated debug sensor setup
    Also created settings print function
2021-01-04 Fixed Vishnu's mess by commenting it out
    [acquisition.c]
2021-01-09 Fixed linked list creation and updated controlLogic outline
    [common.h]
2021-01-10 Trying to get stable build in CubeMX
    Error Message:
    C:/Users/Jeff/Documents/GitHub/AnR/MITCH_2021/Debug/../Src/sysmem.c:55: multiple definition of `_sbrk'
    Src/syscalls.o:C:/Users/Jeff/Documents/GitHub/AnR/MITCH_2021/Debug/../Src/syscalls.c:118: first defined here
    startup/startup_stm32f429zitx.o:(.isr_vector+0x0): multiple definition of `g_pfnVectors'
    startup/startup_stm32f429xx.o:(.isr_vector+0x0): first defined here
    startup/startup_stm32f429zitx.o: In function `DMA2D_IRQHandler':
    C:/Users/Jeff/Documents/GitHub/AnR/MITCH_2021/Debug/../startup/startup_stm32f429zitx.s:111: multiple definition of `Default_Handler'
    startup/startup_stm32f429xx.o:C:/Users/Jeff/Documents/GitHub/AnR/MITCH_2021/Debu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
    [acquisition.c, common.h]
2021-01-10 Revert "Updated Project Settings"
    This reverts commit 26fb79c6fef0c98073ad5025317dcc7857182b26.
    [MITCH_2021.ioc, main.c]
2021-01-10 Revert "Revert "Updated Project Settings""
    This reverts commit 479d4205e1e0c8f1c99ee10e338188257269b593.
    [MITCH_2021.ioc, main.c]
2021-01-10 Made build stable in both Eclipse and STM32 IDE
2021-01-11 Continued setting up GPIO for adc
2021-01-14 Commonized sendSPI and recieveSPI to allow for both SPI busses to be used
2021-01-16 Updated Battery Voltage
2021-01-18 Updated imu struct and processing to better reflect aquired data
    Renamed struct members to reflect register names
    Changed types from floats to ints
    Added constants to divide with within processing
2021-01-19 Moved NDEBUG definition to main.h, so it no longer had to be commented/uncommented
    [common.h, main.h]
2021-01-20 Fixed cast warnings when using testbed
    [monitoring.c]
2021-01-26 Fixed infinite loop induced by testbed
    [acquisition.c]
2021-01-26 fixed infinite loop induced by testbed in other spot
    [acquisition.c]
2021-01-26 fix nmea erasing logic
    [acquisition.c]
2021-01-28 Overhauled print marcros
2021-01-28 Removed print artifacts
2021-01-28 Corrected Nucleo project location
    [acquisition.c, common.h]
2021-01-30 Added in storage function prototypes and began preparations for testbed
2021-02-01 Weeded out hardware inclusion errors
    [acquisition.c, genericInterface.c, genericInterface.h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]
2021-02-01 Added spi inclusion to generic interface
2021-02-03 Created Bank and LED constructors
2021-02-06 Avionics Bay
    [90322A656_HIGH-STRENGTH STEEL THREADED ROD.SLDPRT, 90596A111.SLDPRT, 90596A111_STEEL ROUND-BASE WELD NUT.SLDPRT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]
2021-02-07 Added PCB Files
    [PSPS_AVNC_SRD_central-2020-09-19.brd, PSPS_AVNC_SRD_central-2020-09-19.sch, PSPS_AVNC_SRD_central-2020-09-28.brd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]

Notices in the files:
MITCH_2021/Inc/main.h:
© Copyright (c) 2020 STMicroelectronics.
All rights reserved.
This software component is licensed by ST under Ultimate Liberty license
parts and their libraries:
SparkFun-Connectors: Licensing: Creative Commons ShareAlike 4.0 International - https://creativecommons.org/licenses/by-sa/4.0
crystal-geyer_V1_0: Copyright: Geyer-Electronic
